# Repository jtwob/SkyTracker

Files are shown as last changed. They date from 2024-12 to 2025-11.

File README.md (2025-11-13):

# The SkyTracker v3

Skytracker v3 Prototype
This is the functional 16:1 belt gear box designed to supply steady controllable rotation to a camera (eventually a telescope).

Skytracker v3 Open
This is the internal assembly.

## Impetus

I began this project shortly after embarking into my hobby of amateur astronomy. Sky-tracking telescopes are a bit expensive, and I had a simple analogue telescope. I decided it would be more economical to build my own. This v3 is designed to work with my camera, with further iterations planned to allow me to mount my telescope, and ultimately record and control the telescope view remotely with a Raspberry Pi and additional motors.

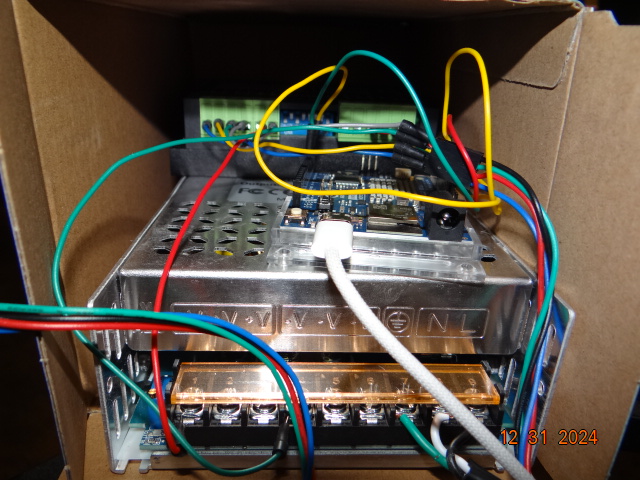
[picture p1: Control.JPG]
Control System


## Design

This features a simple stepper motor driven by a microstep driver and Arduino. It is rigged up to some standard belt pulleys at a rev reduction of 16:1. The reason for this was that the v1 with the stepper alone did not offer enough microsteps to smoothly track distant objects (25600steps/rev), it worked out to approximately 1 step per 4 seconds, i.e. ~60 arcseconds per step. The sky appears to rotate about us at a rate of 15 arcseconds per second, and I had to overcompensate for the size of the individual pixel sensors in my camera such that the movement would not create too much streaking during long exposure photography. The belt pulleys added in v2 offer 16x the steps per second by operating the motor 16x faster with the same 25600 steps per revolution, translating to about ~3.75 arcseconds per step, and it looks smooth! The tension in the belt pulley design has the double benefit of removing the majority of the jitter in the shot due to the choppy nature of stepper motors. In v3 I designed a gearbox with bearings at two points on each pulley axle so that the leverage presented into the v2 by the weight of the sensor (in this case my camera, eventually the telescope) does not bend the assembly out of alignment with the target or alignment with celestial north.

## How it works

The v3 is controlledby an Arduino that holds the timing instructions and translating into motor impulse controls for a microstep driver. The driver supplies the correct power and impulses to the motor so that it rotates 16 times in 24 hours. The power supply is 24V, 25A, 600W DC, and provides power to the motor vis-a-vis the driver. My prototype is rigged up so that I can plug it into wall power and it will begin operating automatically.

### Viewing Celestial Bodies

In order to use this device effectively, the rotation axis must be pointing directly at Polaris so that it co-rotates with the sky. I intend to create easier sighting mechanisms than the current method of eyeballing the lineup, perhaps a small magnification crosshair scope. Eventually I hope to mount the whole assembly on a motorized swivel so that alignment can also be automated. After that, it is simply a matter of pointing the camera at the desired target.

## The SkyTracker v2

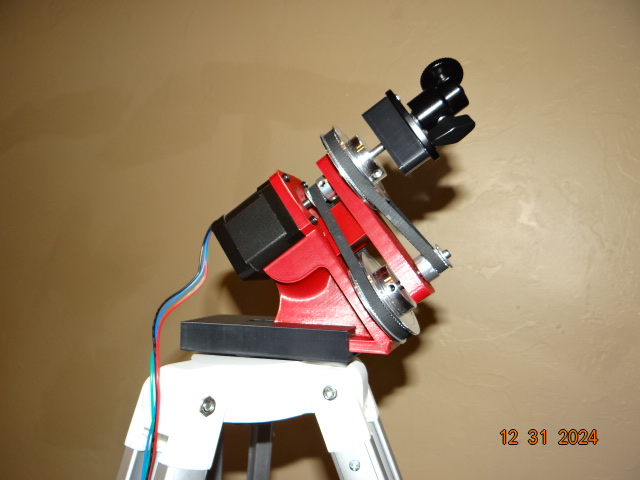
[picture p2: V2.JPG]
SkyTracker v2 Prototype


I managed to take a few pictures with the V2, but it was quite difficult to target properly due to the lever mechanics of the design mentioned previously. The best image I was able to capture is included below, and it features Orion's Belt, with the top of the Orion Nebula cutoff at the bottom of the photo.

Orion's Belt

## The SkyTracker v1

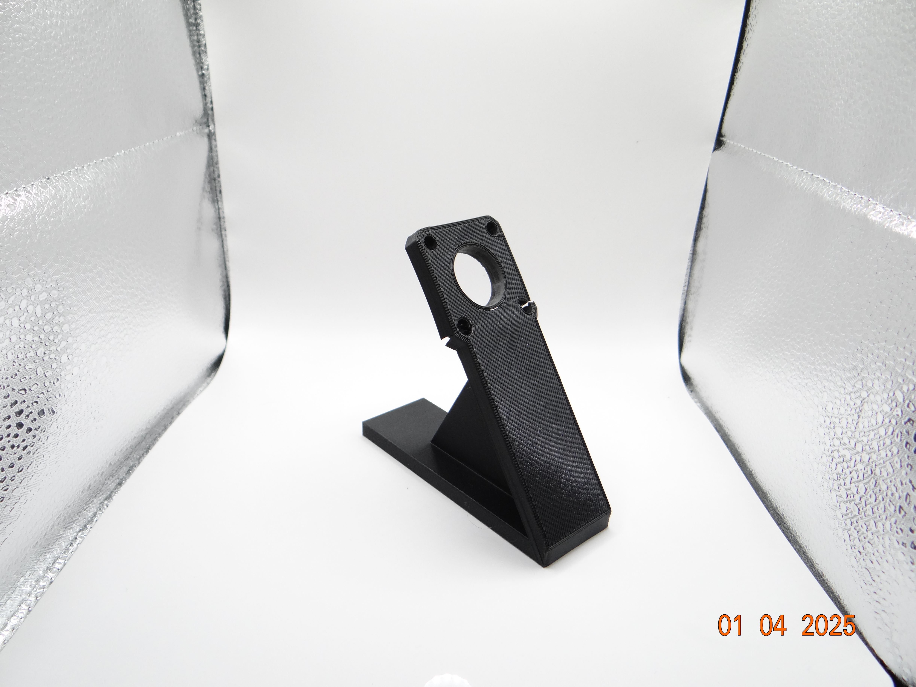
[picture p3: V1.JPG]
SkyTracker v1 Prototype


You may notice the fractures in this picture and these were caused by heat buildup in the motor melting the PLA. I was conducting an endurance test at the time as to how long the system could keep the Moon centered in frame. The rig worked for several hours until the moon was visibly not centered on screen. This let me know I had my targeting correct, but it was far too jittery, and in the end, melted the mount.

## Author

**James**  
Creator and amateur astronomer. This project is part of my ongoing exploration of DIY solutions to enhance my stargazing hobby.

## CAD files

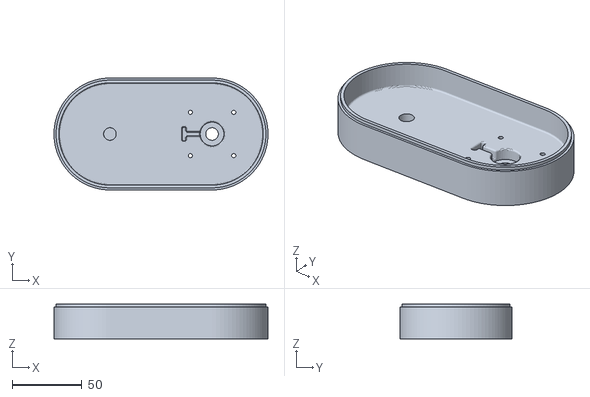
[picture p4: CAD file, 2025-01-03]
beltgearboxv1/Beltbox_base v1 v9.stl
152.9 x 80.0 x 25.0

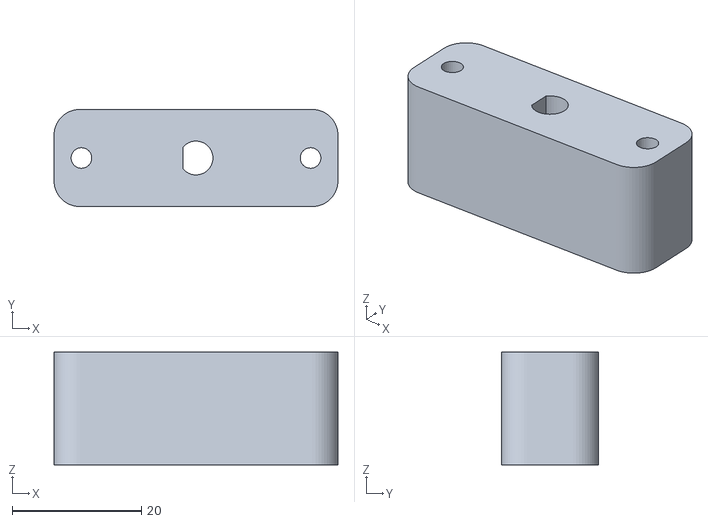
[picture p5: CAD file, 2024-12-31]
bracketholder/CameraMountAdapter_v1.stl
44.0 x 15.1 x 17.5

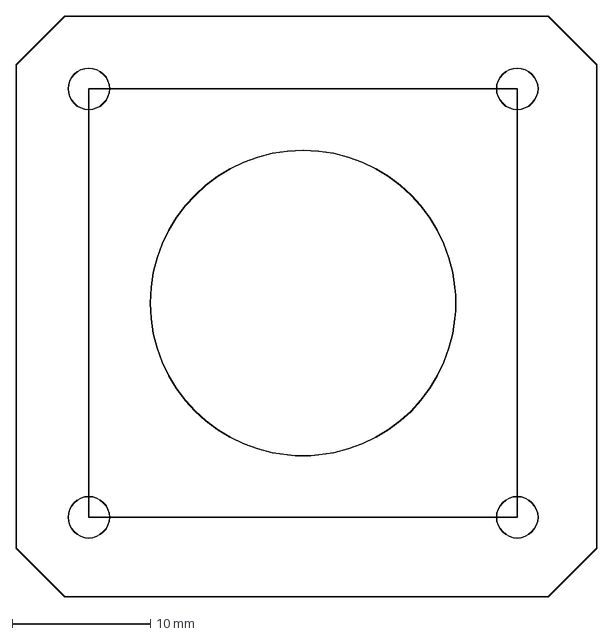
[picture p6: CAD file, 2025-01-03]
MotorDims.dxf
42.0 x 42.0 mm

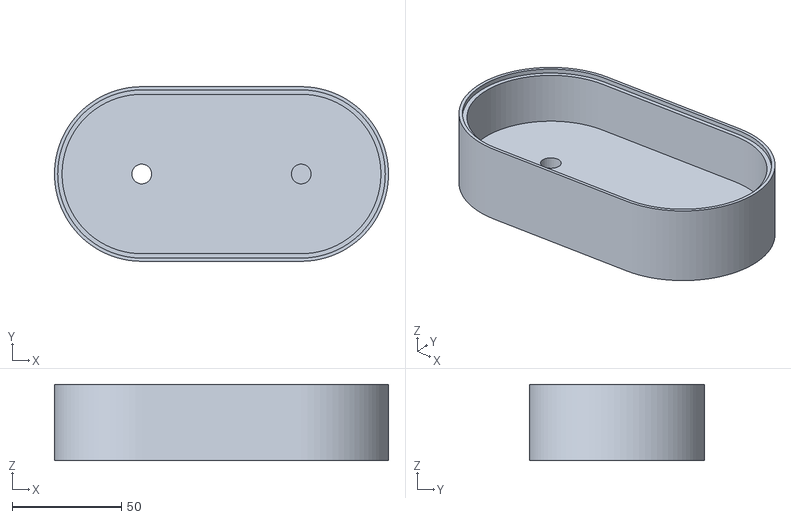
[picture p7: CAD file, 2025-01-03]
beltgearboxv1/Beltbox_top v1 v3.stl
152.9 x 80.0 x 35.0

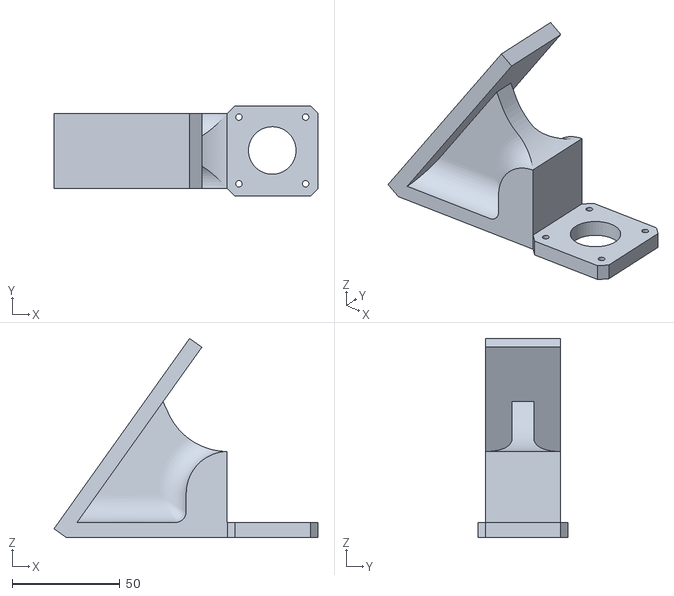
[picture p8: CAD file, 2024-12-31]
bracketholder/StepperAngledMount_v2.stl
122.7 x 42.0 x 92.5

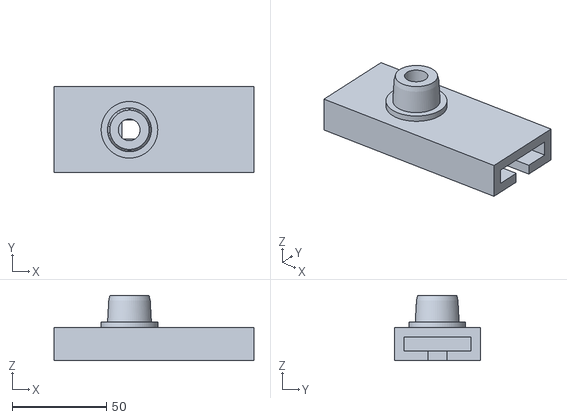
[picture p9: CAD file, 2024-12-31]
Mount-TripodAdapter_v1.stl
106.0 x 45.5 x 34.5

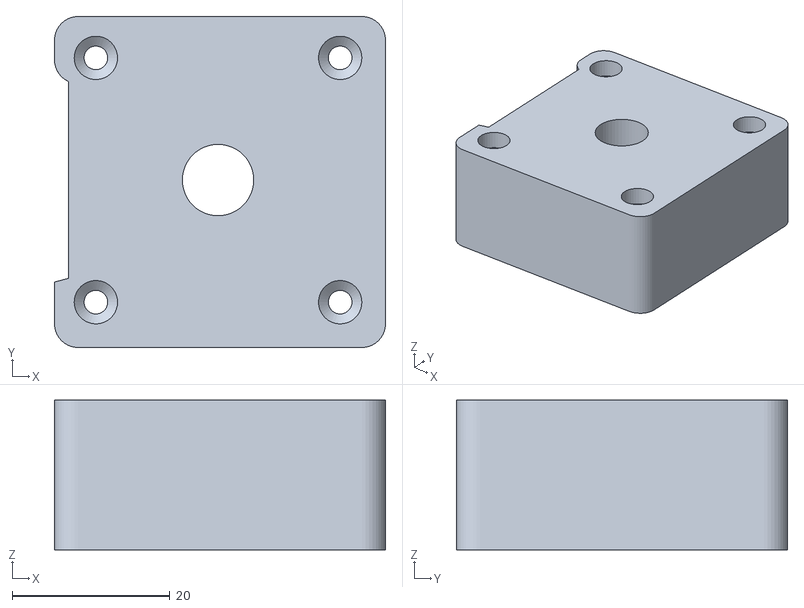
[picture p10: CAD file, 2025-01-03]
beltgearboxv1/BearingHolder v1.stl
42.0 x 42.0 x 19.0

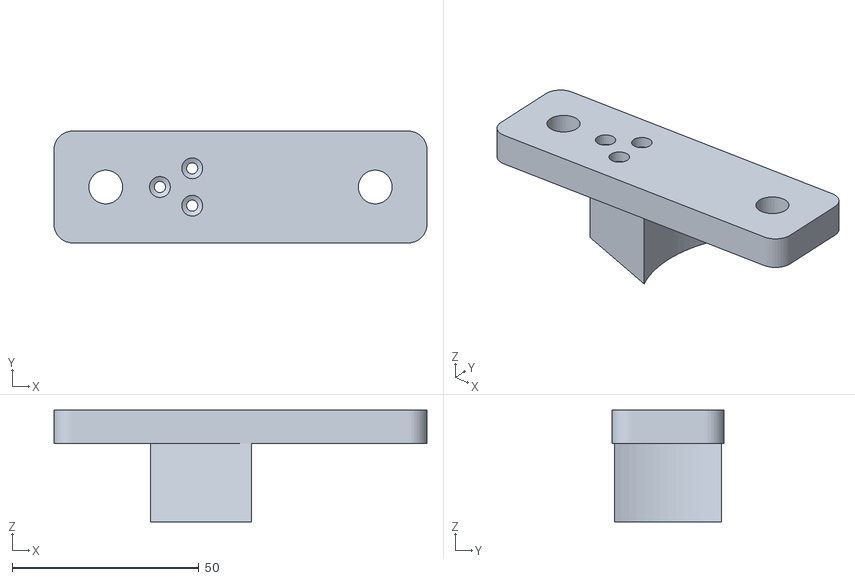
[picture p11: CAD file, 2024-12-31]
bracketholder/BeltPulleyBracket_v2.stl
100.0 x 30.0 x 30.0

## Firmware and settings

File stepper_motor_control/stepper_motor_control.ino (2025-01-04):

// Define pins for the stepper driver
#define STEP_PIN 3 // Connect to PUL+
#define DIR_PIN 4  // Connect to DIR+
//#define ENABLE_PIN 7 // Optional, connect to ENABLE+ if your driver supports it

// Stepper motor settings
int stepsPerRevolution = 25600; // Adjust according to your motor's specs
int speedDelay = 1;        // Microseconds between steps (adjust for speed)
int dayLen = 86400;

void setup() {
  // Set pin modes
  pinMode(STEP_PIN, OUTPUT);
  pinMode(DIR_PIN, OUTPUT);
}

void loop() {
  // // Rotate once per day
  digitalWrite(DIR_PIN, HIGH); // Set direction to clockwise
  stepMotor();
  delay(dayLen*1000/(stepsPerRevolution*16)); 

  //Rotate counterclockwise
  // digitalWrite(DIR_PIN, LOW); // Set direction to counterclockwise
  // for (int i = 0; i < stepsPerRevolution*16; i++) {
  //   stepMotor();
  // }
  // delay(1000); // Pause for 1 second
}

// Function to take a single step
void stepMotor() {
  digitalWrite(STEP_PIN, HIGH);
  delayMicroseconds(speedDelay); // Wait for step duration
  digitalWrite(STEP_PIN, LOW);
  delayMicroseconds(speedDelay); // Wait for step duration
}

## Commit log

2024-12-31 STL files for the mount system
    [BeltPulleyBracket_v2.stl, StepperAngledMount_v2.stl]
2024-12-31 Consolidated the rest of the existing parts for the skytracker
    [CameraMountAdapter_v1.stl, Mount-TripodAdapter_v1.stl]
2025-01-03 Prototype V3 Gearbox
    [BearingHolder v1.stl, BeltPulleyBracket_v2.stl, Beltbox_base v1 v9.stl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]
2025-01-04 Adjusted motor control
2025-11-13 Clarify design details in README
    Updated the description of the design section to clarify the purpose of the gearbox and its impact on alignment.
